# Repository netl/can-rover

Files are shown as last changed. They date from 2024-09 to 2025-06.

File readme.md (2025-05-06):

# can-rover

The goal is to convert cheap RC car kits in to computer driven robots by
replacing the receiver with a separate module.  
The project consists of three parts working as a whole:

1. [Hardware](#hardware)
2. [Firmware](#firmware)
3. [ROS2 node](#ros2-node)

## Hardware

features:

* XT60 passthrough
* fuse protected battery input
* battery current & voltage measurement
    * maximum rating: 20 V, 30 A
    * a charge current of 10 A max can be measured
* 2x canbus+power connectors
* 8 buffered servo channels
* 8 selectable addresses
* 8 buffered inputs with pull-up to 5V
* e-stop controlled servo power

### CAN header

Jumper for 120R termination.  
May be used to power low power stuff. Connector rated at 3 A.  

|pin|  signal |
|---|---|
| 1 | GND |
| 2 | Battery |
| 3 | CAN\_L  |
| 4 | CAN\_H  |

## Firmware

* can-utils: `sudo ip link set up can0 type can bitrate 500000`
* All messages are `big-endian`. 
* [python-can](https://python-can.readthedocs.io/en/stable/scripts.html) has great tools for debugging.
* build with `cd firmware; make`

### CAN messages

`base_address` is selectable by rotary switch. All messages have an offset from that address.
```c
uint8_t arbitration_id = base_address << 8; // address 0 would be: 0x000 and 7: 0x070
```

offset  |parameter       |I/O|bytes
--------|----------------|---|-----
0x0     | servo 1        | I | 1
...     | servo ...      | I | 1
0x7     | servo 8        | I | 1
0x8     | battery Voltage| O | 2
0x9     | battery Current| O | 2
0xa     | sensors 1 .. 8 | O | 1

### Servo

PWM in `1 µs` resolution and if channel hasn't been set within `1 s` it will default to `1500 µs`. For example: `servo 3` with `base_address = 5` would be set to `-90°` with:

```bash
$ cansend can0 052#3e8
```

### Battery monitor

Analog signals directly from A/D, maximum: `4095`

### Inputs

One byte where each bit represents an input

```c
bool value = inputs >> n-1 & 0x1;
```

## ROS2 node
Provided node bridges firmware to ros topics.

### Installation

1. Install [ROS2](https://docs.ros.org/en/jazzy/Installation.html)
2. create [ros2_ws](https://docs.ros.org/en/jazzy/Tutorials/Beginner-Client-Libraries/Creating-A-Workspace/Creating-A-Workspace.html)

```bash
apt install python3-rosdep python3-colcon-common-extensions
ln -s ros2_can_rover ~/ros2_ws/src/can_rover
cd ~/ros2_ws/
colcon build
source install/setup.bash
rosdep init
rosdep update
rosdep install --from-paths src -y --ignore-src
ros2 run can_rover can_rover
```

### Topics and parameters

Interfaces provided are bare minimum for simplicity

topic                      |type     |publish / subscribe|min   |max  |
---------------------------|---------|-------------------|------|-----|
`/rover/voltage`           |[Float32]|subscribe          |0   \*|20\* |
`/rover/current`           |[Float32]|subscribe          |-10 \*|30\* |
`/rover/watts`             |[Float32]|subscribe          |-200\*|600\*|
`/rover/wattHours`         |[Float32]|publish & subscribe|      |     |
`/rover/channel_<n>`       |[Float32]|publish            | -1   | 1   |
`/rover/input_<n>`         |[Bool]   |subscribe          | 0    | 1   |

*\*min/max values limited hardware tolerances and calibration*

parameter                  |type     |default   |
---------------------------|---------|----------|
`/rover/voltage_scale`     |[Float32]|20 / 2^12 |
`/rover/voltage_offset`    |[Float32]|0         |
`/rover/current_scale`     |[Float32]|-40 / 2^12|
`/rover/current_offset`    |[Float32]|10        |
`/rover/channel_<n>_scale` |[Float32]|500       |
`/rover/channel_<n>_offset`|[Float32]|1500      |

[Float32]:https://github.com/ros2/example_interfaces/blob/master/msg/Float32.msg
[Bool]:https://github.com/ros2/example_interfaces/blob/master/msg/Bool.msg

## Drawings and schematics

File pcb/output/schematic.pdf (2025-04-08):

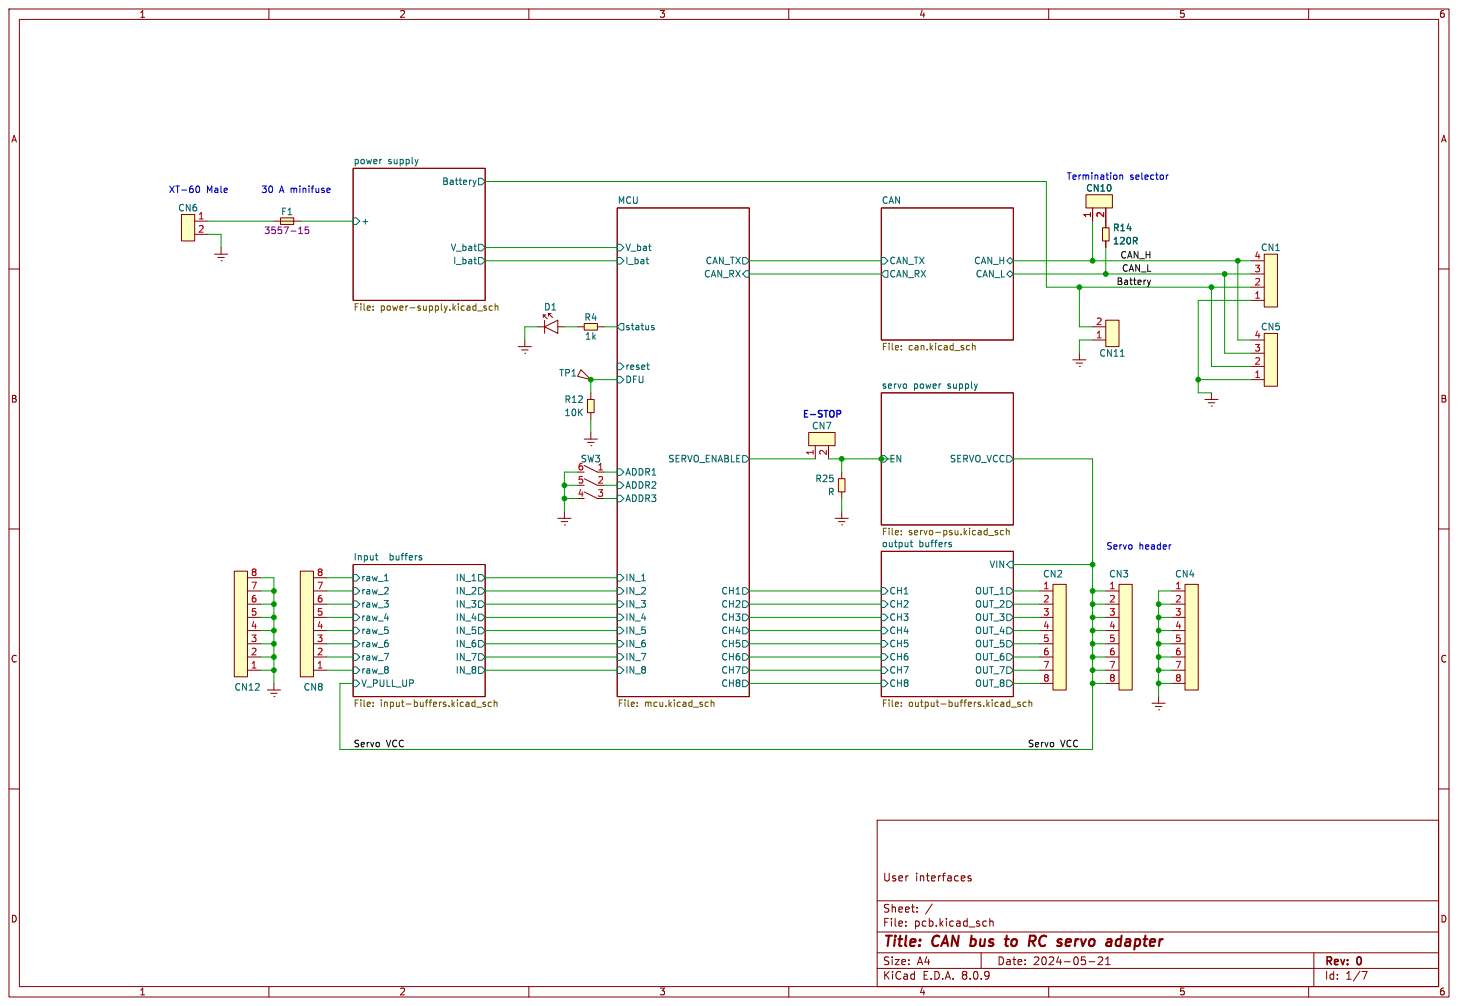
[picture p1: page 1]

output buffers File: output-buffers.kicad_sch

Id: 1/7 Title: CAN bus to RC servo adapter File: pcb.kicad_sch Sheet: / User interfaces

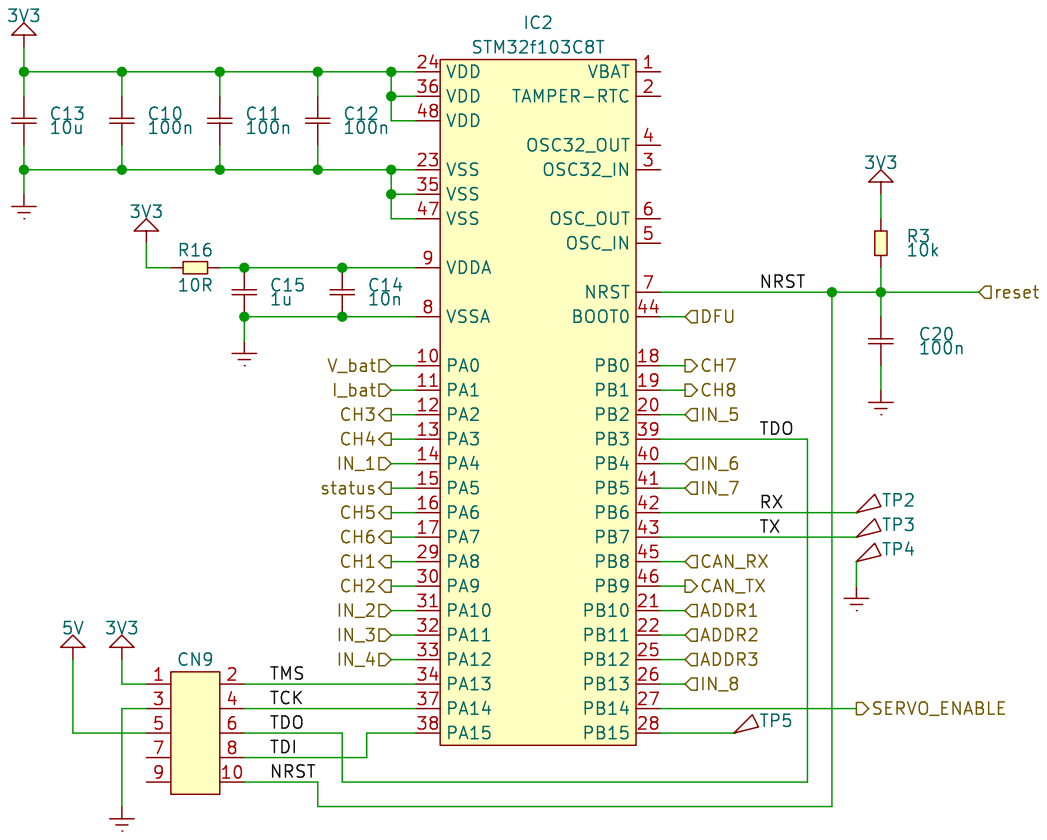
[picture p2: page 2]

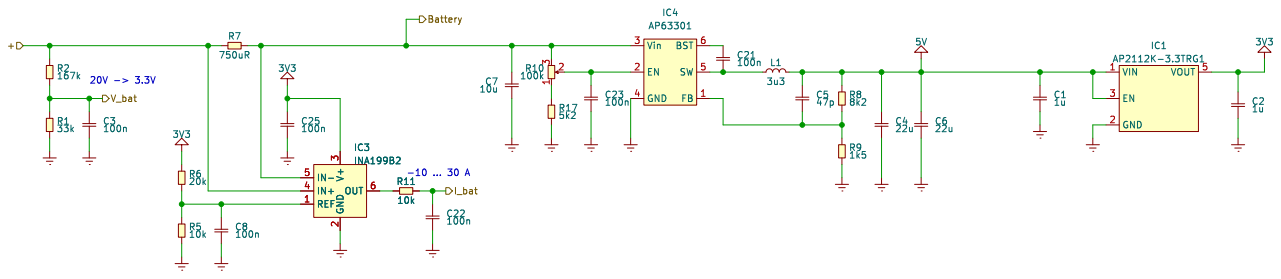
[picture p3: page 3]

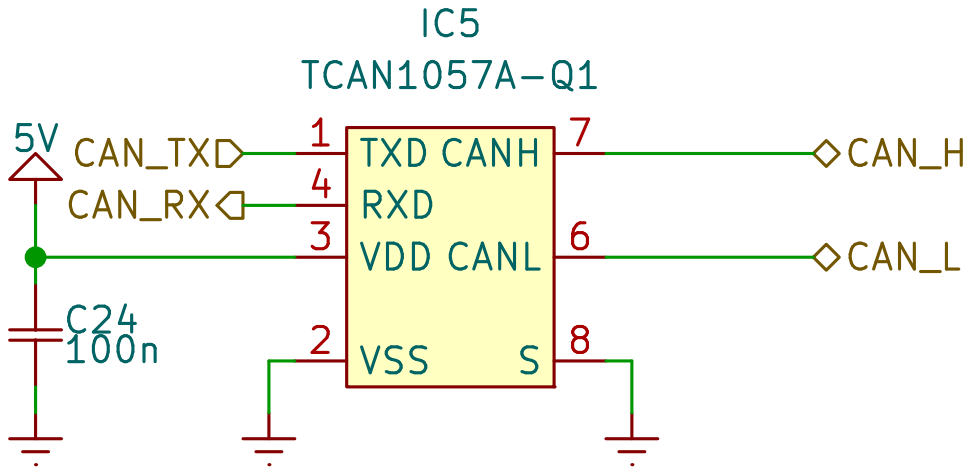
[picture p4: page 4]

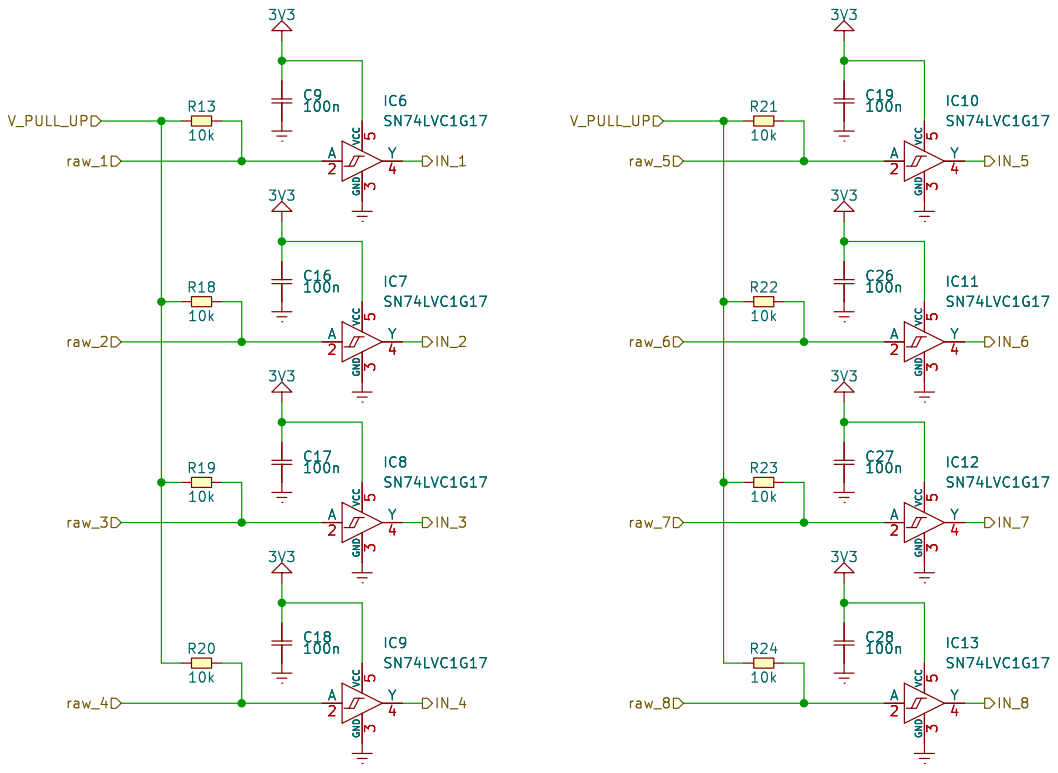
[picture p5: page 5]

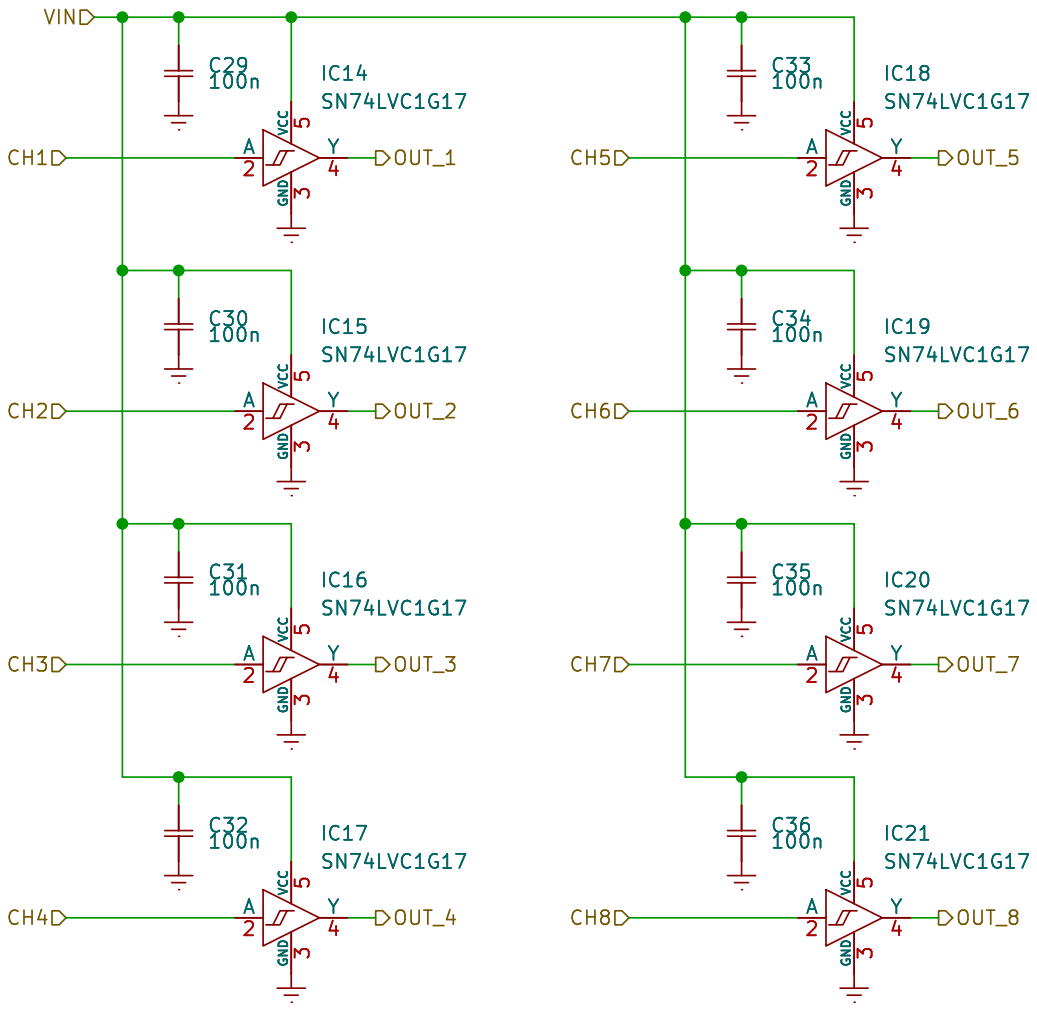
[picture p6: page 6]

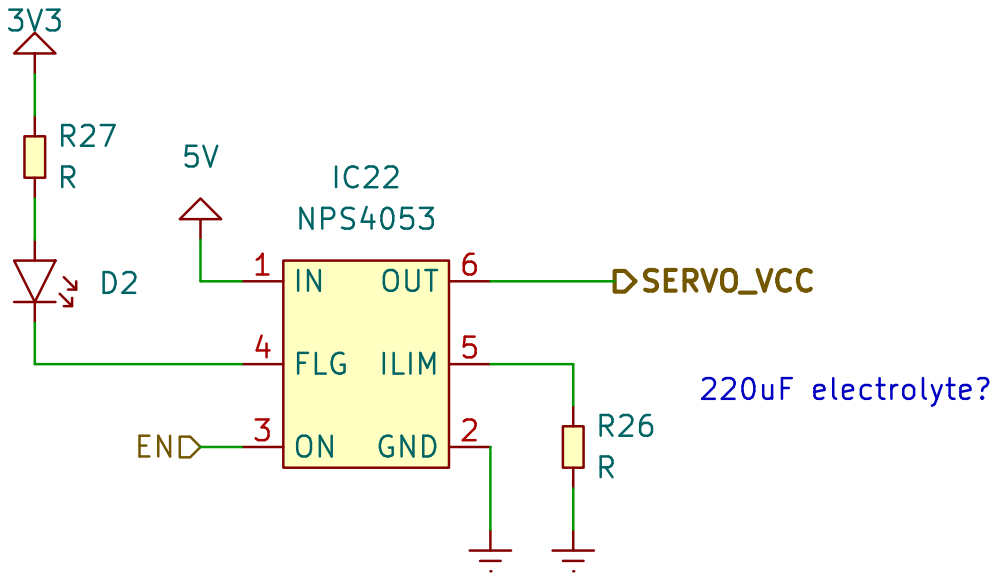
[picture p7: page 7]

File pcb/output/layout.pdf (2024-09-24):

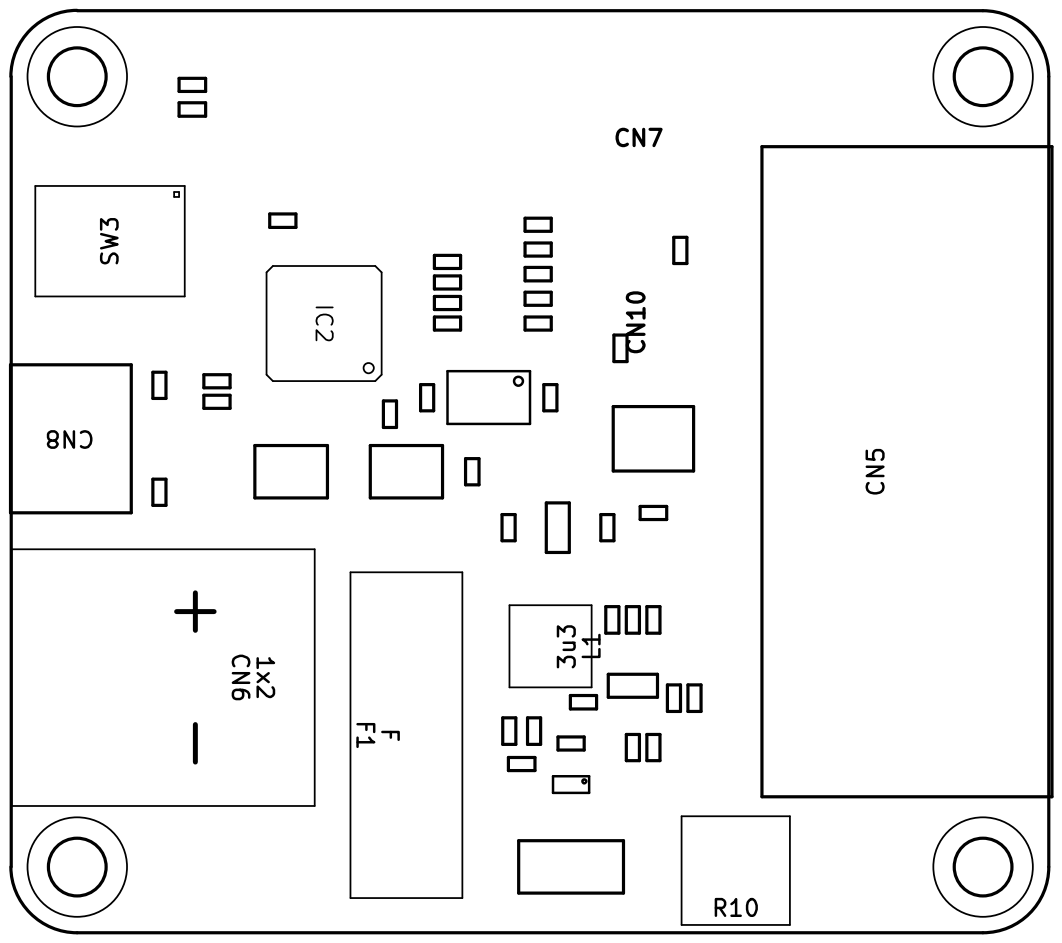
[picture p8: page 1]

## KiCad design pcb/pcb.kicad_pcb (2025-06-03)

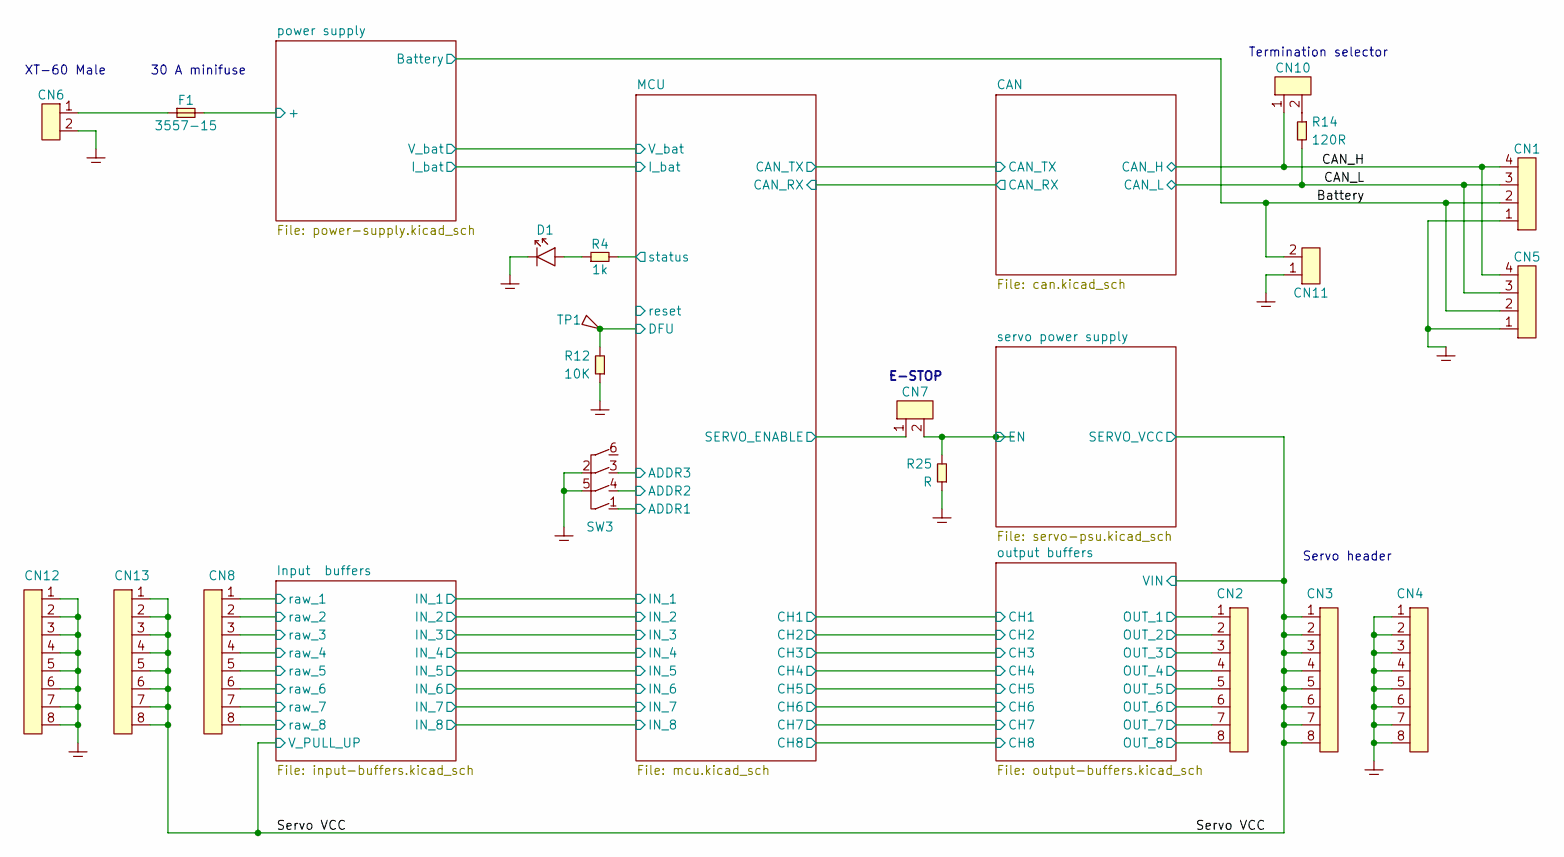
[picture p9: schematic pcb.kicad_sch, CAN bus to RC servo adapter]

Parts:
CN1, CN5: 1x4; jst-xh-4; MPN B4B-XH-A; DigiKey 455-B4B-XH-A-ND
CN2, CN3, CN4, CN8, CN12, CN13: 1x8
CN6, CN11: 1x2; XT60
CN7, CN10: 1x2
D1: LED; 0603
F1: F; 3557-15; MPN 3557-15; DigiKey 36-3557-15-ND
R4: 1k; 0603
R12: 10K; 0603
R14: 120R; 0603
R25: R; 0603
SW3: RD10RA8RTT; MPN RD10RA8RTT; Digi-Key 2449-RD10RA8RTT-ND
TP1: test_point

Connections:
/Battery: CN1.2, CN5.2, CN11.2; also elsewhere on the board
/CAN_H: CN1.4, CN5.4, CN10.1; also elsewhere on the board
/CAN_L: CN1.3, CN5.3, R14.2; also elsewhere on the board
/Input buffers/raw_1: CN8.1; also elsewhere on the board
/Input buffers/raw_2: CN8.2; also elsewhere on the board
/Input buffers/raw_3: CN8.3; also elsewhere on the board
/Input buffers/raw_4: CN8.4; also elsewhere on the board
/Input buffers/raw_5: CN8.5; also elsewhere on the board
/Input buffers/raw_6: CN8.6; also elsewhere on the board
/Input buffers/raw_7: CN8.7; also elsewhere on the board
/Input buffers/raw_8: CN8.8; also elsewhere on the board
/MCU/ADDR1: SW3.1; also elsewhere on the board
/MCU/ADDR2: SW3.4; also elsewhere on the board
/MCU/ADDR3: SW3.3; also elsewhere on the board
/MCU/DFU: R12.2, TP1.1 (TP); also elsewhere on the board
/MCU/SERVO_ENABLE: CN7.1; also elsewhere on the board
/MCU/status: R4.2; also elsewhere on the board
/Servo VCC: CN3.1, CN3.2, CN3.3, CN3.4, CN3.5, CN3.6, CN3.7, CN3.8, CN13.1, CN13.2, CN13.3, CN13.4, CN13.5, CN13.6, CN13.7, CN13.8; also elsewhere on the board
/output buffers/OUT_1: CN2.1; also elsewhere on the board
/output buffers/OUT_2: CN2.2; also elsewhere on the board
/output buffers/OUT_3: CN2.3; also elsewhere on the board
/output buffers/OUT_4: CN2.4; also elsewhere on the board
/output buffers/OUT_5: CN2.5; also elsewhere on the board
/output buffers/OUT_6: CN2.6; also elsewhere on the board
/output buffers/OUT_7: CN2.7; also elsewhere on the board
/output buffers/OUT_8: CN2.8; also elsewhere on the board
/power supply/+: F1.2; also elsewhere on the board
/servo power supply/EN: CN7.2, R25.2; also elsewhere on the board
GND: CN1.1, CN4.1, CN4.2, CN4.3, CN4.4, CN4.5, CN4.6, CN4.7, CN4.8, CN5.1, CN6.2, CN11.1, CN12.1, CN12.2, CN12.3, CN12.4, CN12.5, CN12.6, CN12.7, CN12.8, D1.2 (K), R12.1, R25.1, SW3.2, SW3.5; also elsewhere on the board
unnamed: CN6.1, F1.1
unnamed: CN10.2, R14.1
unnamed: D1.1 (A), R4.1

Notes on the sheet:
30 A minifuse
E-STOP
Termination selector
Servo header
XT-60 Male

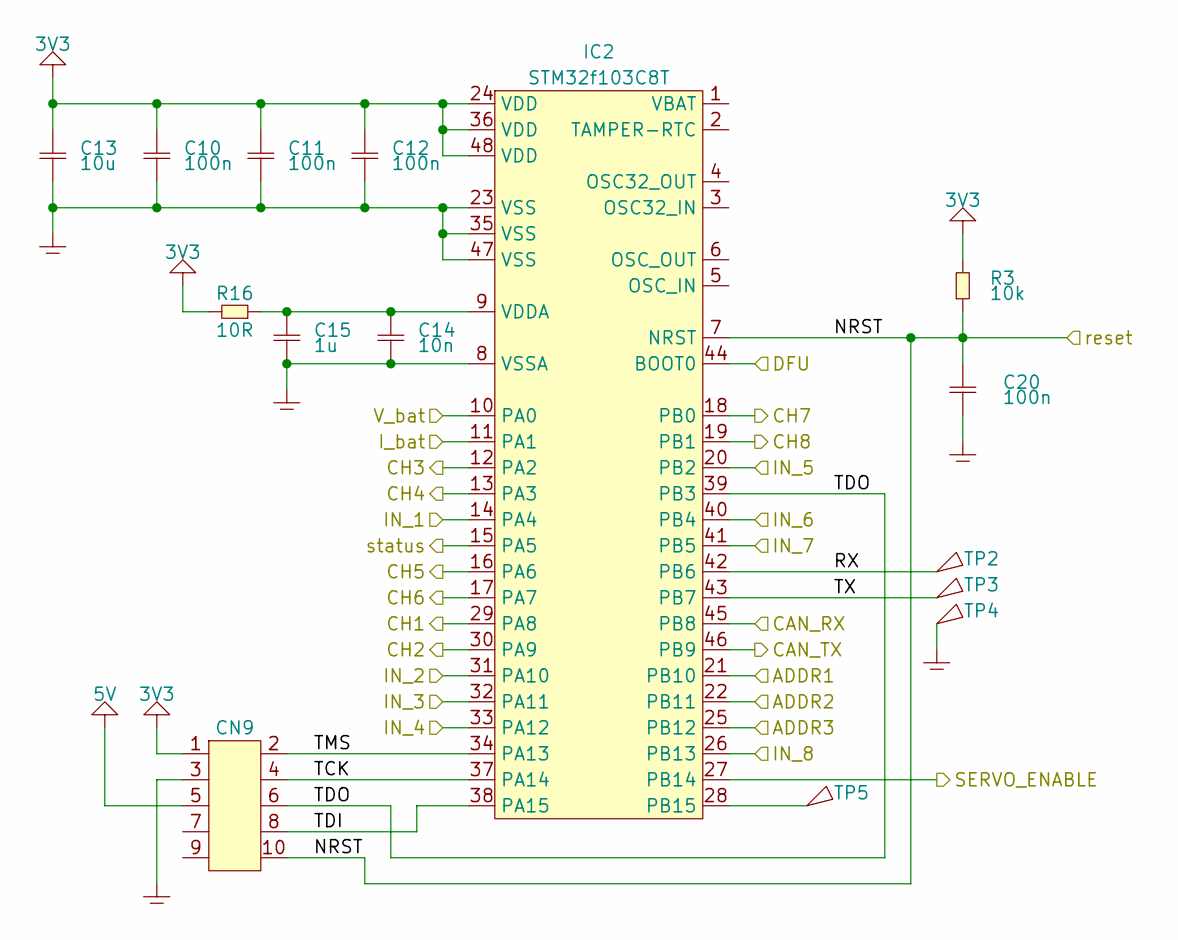
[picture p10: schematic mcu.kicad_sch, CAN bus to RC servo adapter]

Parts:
C10, C11, C12, C20: 100n; 0603
C13: 10u; 0603
C14: 10n; 0603
C15: 1u; 0603
CN9: 2x5; 2x5_test_points
IC2: STM32f103C8T; LQFP-48; MPN STM32F103C8T6TR; DigiKey 497-17666-1-ND
R3: 10k; 0603
R16: 10R; 0603
TP2, TP3, TP4, TP5: test_point

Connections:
3V3: C10.1, C11.1, C12.1, C13.1, CN9.1, IC2.24 (VDD), IC2.36 (VDD), IC2.48 (VDD), R3.2, R16.2; also elsewhere on the board
5V: CN9.5; also elsewhere on the board
/CAN/CAN_RX: IC2.45 (PB8); also elsewhere on the board
/CAN/CAN_TX: IC2.46 (PB9); also elsewhere on the board
/Input buffers/IN_1: IC2.14 (PA4); also elsewhere on the board
/Input buffers/IN_2: IC2.31 (PA10); also elsewhere on the board
/Input buffers/IN_3: IC2.32 (PA11); also elsewhere on the board
/Input buffers/IN_4: IC2.33 (PA12); also elsewhere on the board
/Input buffers/IN_5: IC2.20 (PB2); also elsewhere on the board
/Input buffers/IN_6: IC2.40 (PB4); also elsewhere on the board
/Input buffers/IN_7: IC2.41 (PB5); also elsewhere on the board
/Input buffers/IN_8: IC2.26 (PB13); also elsewhere on the board
/MCU/ADDR1: IC2.21 (PB10); also elsewhere on the board
/MCU/ADDR2: IC2.22 (PB11); also elsewhere on the board
/MCU/ADDR3: IC2.25 (PB12); also elsewhere on the board
/MCU/CH1: IC2.29 (PA8); also elsewhere on the board
/MCU/CH2: IC2.30 (PA9); also elsewhere on the board
/MCU/CH3: IC2.12 (PA2); also elsewhere on the board
/MCU/CH4: IC2.13 (PA3); also elsewhere on the board
/MCU/CH5: IC2.16 (PA6); also elsewhere on the board
/MCU/CH6: IC2.17 (PA7); also elsewhere on the board
/MCU/CH7: IC2.18 (PB0); also elsewhere on the board
/MCU/CH8: IC2.19 (PB1); also elsewhere on the board
/MCU/DFU: IC2.44 (BOOT0); also elsewhere on the board
/MCU/I_bat: IC2.11 (PA1); also elsewhere on the board
/MCU/NRST: C20.1, CN9.10, IC2.7 (NRST), R3.1
/MCU/RX: IC2.42 (PB6), TP2.1 (TP)
/MCU/SERVO_ENABLE: IC2.27 (PB14); also elsewhere on the board
/MCU/TCK: CN9.4, IC2.37 (PA14)
/MCU/TDI: CN9.8, IC2.38 (PA15)
/MCU/TDO: CN9.6, IC2.39 (PB3)
/MCU/TMS: CN9.2, IC2.34 (PA13)
/MCU/TX: IC2.43 (PB7), TP3.1 (TP)
/MCU/V_bat: IC2.10 (PA0); also elsewhere on the board
/MCU/status: IC2.15 (PA5); also elsewhere on the board
GND: C10.2, C11.2, C12.2, C13.2, C14.2, C15.2, C20.2, CN9.3, IC2.8 (VSSA), IC2.23 (VSS), IC2.35 (VSS), IC2.47 (VSS), TP4.1 (TP); also elsewhere on the board
unnamed: IC2.28 (PB15), TP5.1 (TP)
unnamed: C14.1, C15.1, IC2.9 (VDDA), R16.1

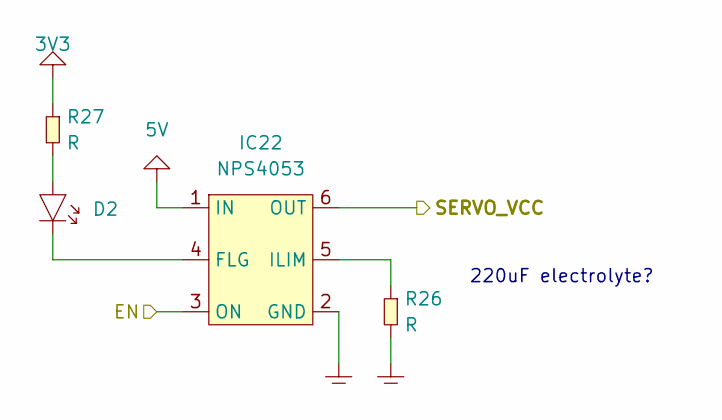
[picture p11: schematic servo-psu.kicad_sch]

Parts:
D2: LED; 0603
IC22: NPS4053; SOT-23-6; MPN NPS4053GVH; DigiKey 1727-NPS4053GVHCT-ND
R26, R27: R; 0603

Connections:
3V3: R27.1; also elsewhere on the board
5V: IC22.1 (IN); also elsewhere on the board
/Servo VCC: IC22.6 (OUT); also elsewhere on the board
/servo power supply/EN: IC22.3 (ON); also elsewhere on the board
GND: IC22.2 (GND), R26.2; also elsewhere on the board
unnamed: D2.1 (A), R27.2
unnamed: D2.2 (K), IC22.4 (FLG)
unnamed: IC22.5 (ILIM), R26.1

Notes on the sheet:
220uF electrolyte?

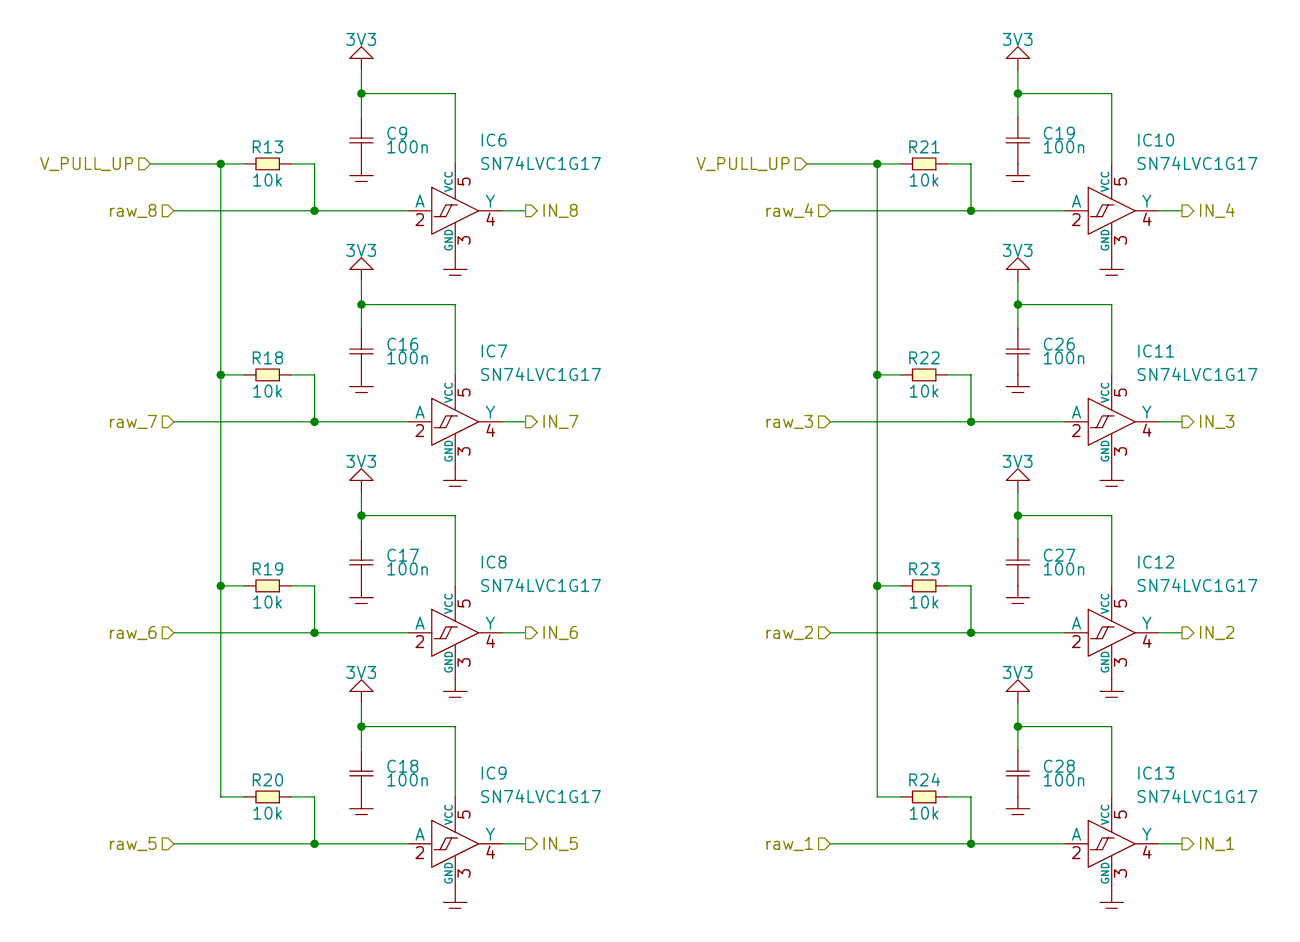
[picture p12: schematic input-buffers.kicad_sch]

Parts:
C9, C16, C17, C18, C19, C26, C27, C28: 100n; 0603
IC6, IC7, IC8, IC9, IC10, IC11, IC12, IC13: SN74LVC1G17; SC70-5L
R13, R18, R19, R20, R21, R22, R23, R24: 10k; 0603

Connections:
3V3: C9.2, C16.2, C17.2, C18.2, C19.2, C26.2, C27.2, C28.2, IC6.5 (VCC), IC7.5 (VCC), IC8.5 (VCC), IC9.5 (VCC), IC10.5 (VCC), IC11.5 (VCC), IC12.5 (VCC), IC13.5 (VCC); also elsewhere on the board
/Input buffers/IN_1: IC13.4 (Y); also elsewhere on the board
/Input buffers/IN_2: IC12.4 (Y); also elsewhere on the board
/Input buffers/IN_3: IC11.4 (Y); also elsewhere on the board
/Input buffers/IN_4: IC10.4 (Y); also elsewhere on the board
/Input buffers/IN_5: IC9.4 (Y); also elsewhere on the board
/Input buffers/IN_6: IC8.4 (Y); also elsewhere on the board
/Input buffers/IN_7: IC7.4 (Y); also elsewhere on the board
/Input buffers/IN_8: IC6.4 (Y); also elsewhere on the board
/Input buffers/raw_1: IC13.2 (A), R24.1; also elsewhere on the board
/Input buffers/raw_2: IC12.2 (A), R23.1; also elsewhere on the board
/Input buffers/raw_3: IC11.2 (A), R22.1; also elsewhere on the board
/Input buffers/raw_4: IC10.2 (A), R21.1; also elsewhere on the board
/Input buffers/raw_5: IC9.2 (A), R20.1; also elsewhere on the board
/Input buffers/raw_6: IC8.2 (A), R19.1; also elsewhere on the board
/Input buffers/raw_7: IC7.2 (A), R18.1; also elsewhere on the board
/Input buffers/raw_8: IC6.2 (A), R13.1; also elsewhere on the board
/Servo VCC: R13.2, R18.2, R19.2, R20.2, R21.2, R22.2, R23.2, R24.2; also elsewhere on the board
GND: C9.1, C16.1, C17.1, C18.1, C19.1, C26.1, C27.1, C28.1, IC6.3 (GND), IC7.3 (GND), IC8.3 (GND), IC9.3 (GND), IC10.3 (GND), IC11.3 (GND), IC12.3 (GND), IC13.3 (GND); also elsewhere on the board

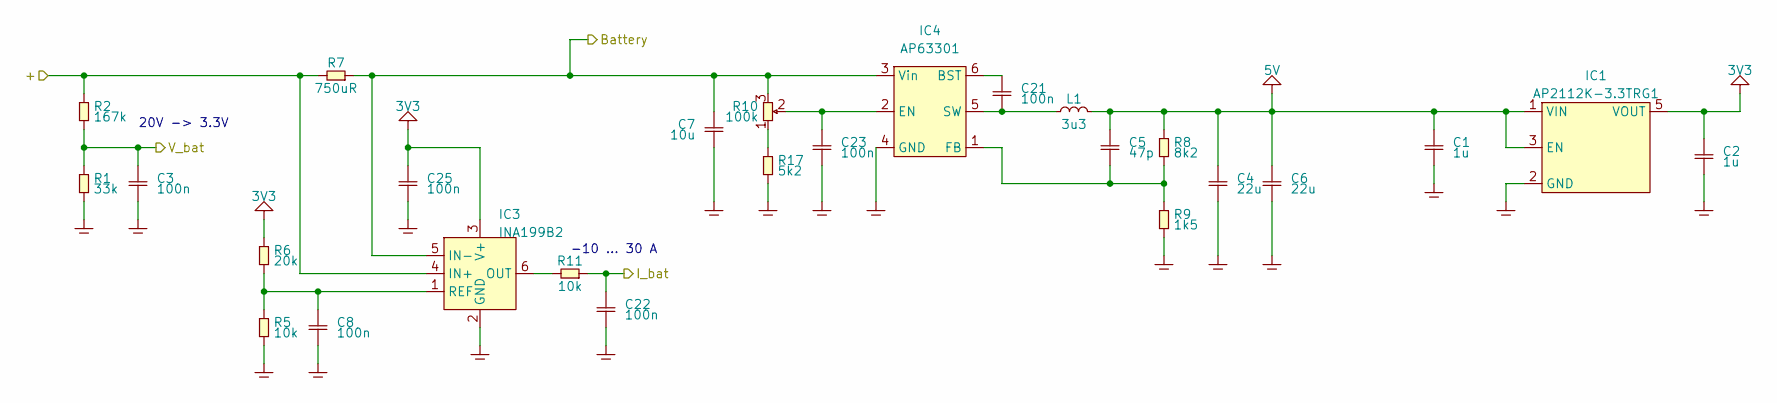
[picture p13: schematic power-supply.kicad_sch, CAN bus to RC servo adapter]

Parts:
C1, C2: 1u; 0603
C3, C8, C21, C22, C23, C25: 100n; 0603
C4, C6: 22u; 0603
C5: 47p; 0603
C7: 10u; 0603
IC1: AP2112K-3.3TRG1; SOT-23-5; MPN AP2112K-3.3TRG1; Digi-Key AP2112K-3.3TRG1DICT-ND
IC3: INA199B2; SC70-6L; MPN INA199B2DCKR; DigiKey 296-40119-1-ND
IC4: AP63301; TSOT-26; MPN AP63301WU-7; DigiKey 31-AP63301WU-7CT-ND
L1: 3u3; 5x5; MPN VLS5045EX-3R3N; DigiKey 445-174398-1-ND
R1: 33k; 0603
R2: 167k; 0603
R5, R11: 10k; 0603
R6: 20k; 0603
R7: 750uR; 2512-high-current
R8: 8k2; 0603
R9: 1k5; 0603
R10: 100k; 3362P; MPN 3362P-1-104LF; DigiKey 3362P-104LF-ND
R17: 5k2; 0603

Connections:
3V3: C2.1, C25.1, IC1.5 (VOUT), IC3.3 (V+), R6.2; also elsewhere on the board
5V: C1.1, C4.1, C5.1, C6.1, IC1.1 (VIN), IC1.3 (EN), L1.2, R8.2; also elsewhere on the board
/Battery: C7.1, IC3.5 (IN-), IC4.3 (Vin), R7.1, R10.3; also elsewhere on the board
/MCU/I_bat: C22.1, R11.1; also elsewhere on the board
/MCU/V_bat: C3.1, R1.2, R2.1; also elsewhere on the board
/power supply/+: IC3.4 (IN+), R2.2, R7.2; also elsewhere on the board
GND: C1.2, C2.2, C3.2, C4.2, C6.2, C7.2, C8.2, C22.2, C23.2, C25.2, IC1.2 (GND), IC3.2 (GND), IC4.4 (GND), R1.1, R5.1, R9.1, R17.1; also elsewhere on the board
unnamed: IC3.6 (OUT), R11.2
unnamed: C8.1, IC3.1 (REF), R5.2, R6.1
unnamed: C21.1, IC4.6 (BST)
unnamed: C23.1, IC4.2 (EN), R10.2
unnamed: C5.2, IC4.1 (FB), R8.1, R9.2
unnamed: C21.2, IC4.5 (SW), L1.1
unnamed: R10.1, R17.2

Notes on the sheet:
-10 ... 30 A
20V -> 3.3V

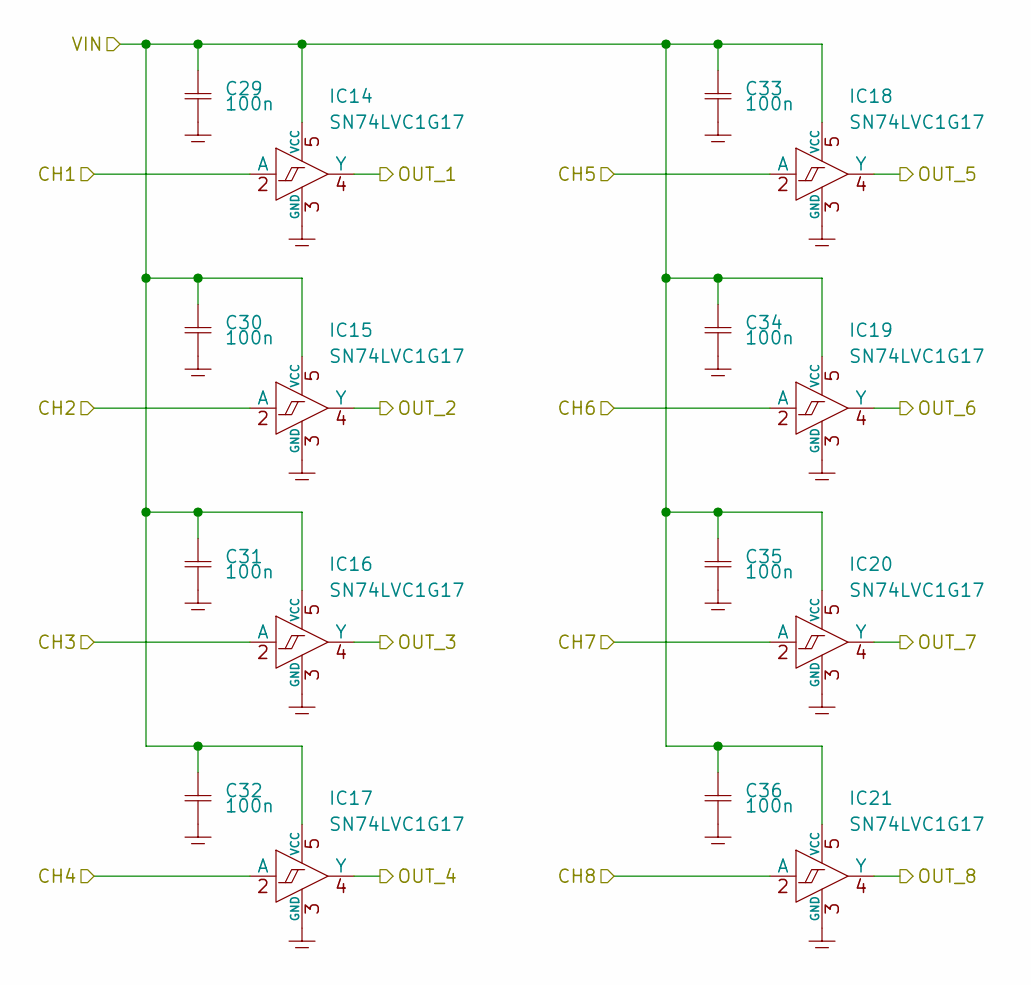
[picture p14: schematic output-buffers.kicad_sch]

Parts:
C29, C30, C31, C32, C33, C34, C35, C36: 100n; 0603
IC14, IC15, IC16, IC17, IC18, IC19, IC20, IC21: SN74LVC1G17; SC70-5L

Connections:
/MCU/CH1: IC14.2 (A); also elsewhere on the board
/MCU/CH2: IC15.2 (A); also elsewhere on the board
/MCU/CH3: IC16.2 (A); also elsewhere on the board
/MCU/CH4: IC17.2 (A); also elsewhere on the board
/MCU/CH5: IC18.2 (A); also elsewhere on the board
/MCU/CH6: IC19.2 (A); also elsewhere on the board
/MCU/CH7: IC20.2 (A); also elsewhere on the board
/MCU/CH8: IC21.2 (A); also elsewhere on the board
/Servo VCC: C29.2, C30.2, C31.2, C32.2, C33.2, C34.2, C35.2, C36.2, IC14.5 (VCC), IC15.5 (VCC), IC16.5 (VCC), IC17.5 (VCC), IC18.5 (VCC), IC19.5 (VCC), IC20.5 (VCC), IC21.5 (VCC); also elsewhere on the board
/output buffers/OUT_1: IC14.4 (Y); also elsewhere on the board
/output buffers/OUT_2: IC15.4 (Y); also elsewhere on the board
/output buffers/OUT_3: IC16.4 (Y); also elsewhere on the board
/output buffers/OUT_4: IC17.4 (Y); also elsewhere on the board
/output buffers/OUT_5: IC18.4 (Y); also elsewhere on the board
/output buffers/OUT_6: IC19.4 (Y); also elsewhere on the board
/output buffers/OUT_7: IC20.4 (Y); also elsewhere on the board
/output buffers/OUT_8: IC21.4 (Y); also elsewhere on the board
GND: C29.1, C30.1, C31.1, C32.1, C33.1, C34.1, C35.1, C36.1, IC14.3 (GND), IC15.3 (GND), IC16.3 (GND), IC17.3 (GND), IC18.3 (GND), IC19.3 (GND), IC20.3 (GND), IC21.3 (GND); also elsewhere on the board

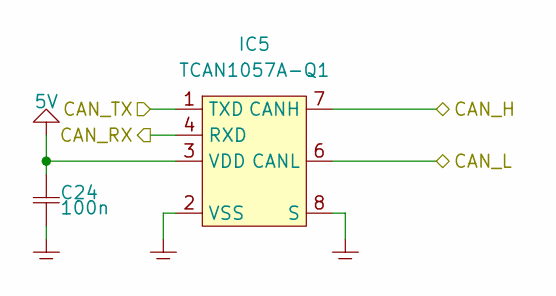
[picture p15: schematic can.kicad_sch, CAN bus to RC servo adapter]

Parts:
C24: 100n; 0603
IC5: TCAN1057A-Q1; TSOT-23-8; MPN TCAN1057AVDDFRQ1; DigiKey 296-TCAN1057AVDDFRQ1CT-ND

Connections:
5V: C24.1, IC5.3 (VDD); also elsewhere on the board
/CAN/CAN_RX: IC5.4 (RXD); also elsewhere on the board
/CAN/CAN_TX: IC5.1 (TXD); also elsewhere on the board
/CAN_H: IC5.7 (CANH); also elsewhere on the board
/CAN_L: IC5.6 (CANL); also elsewhere on the board
GND: C24.2, IC5.2 (VSS), IC5.8 (S); also elsewhere on the board

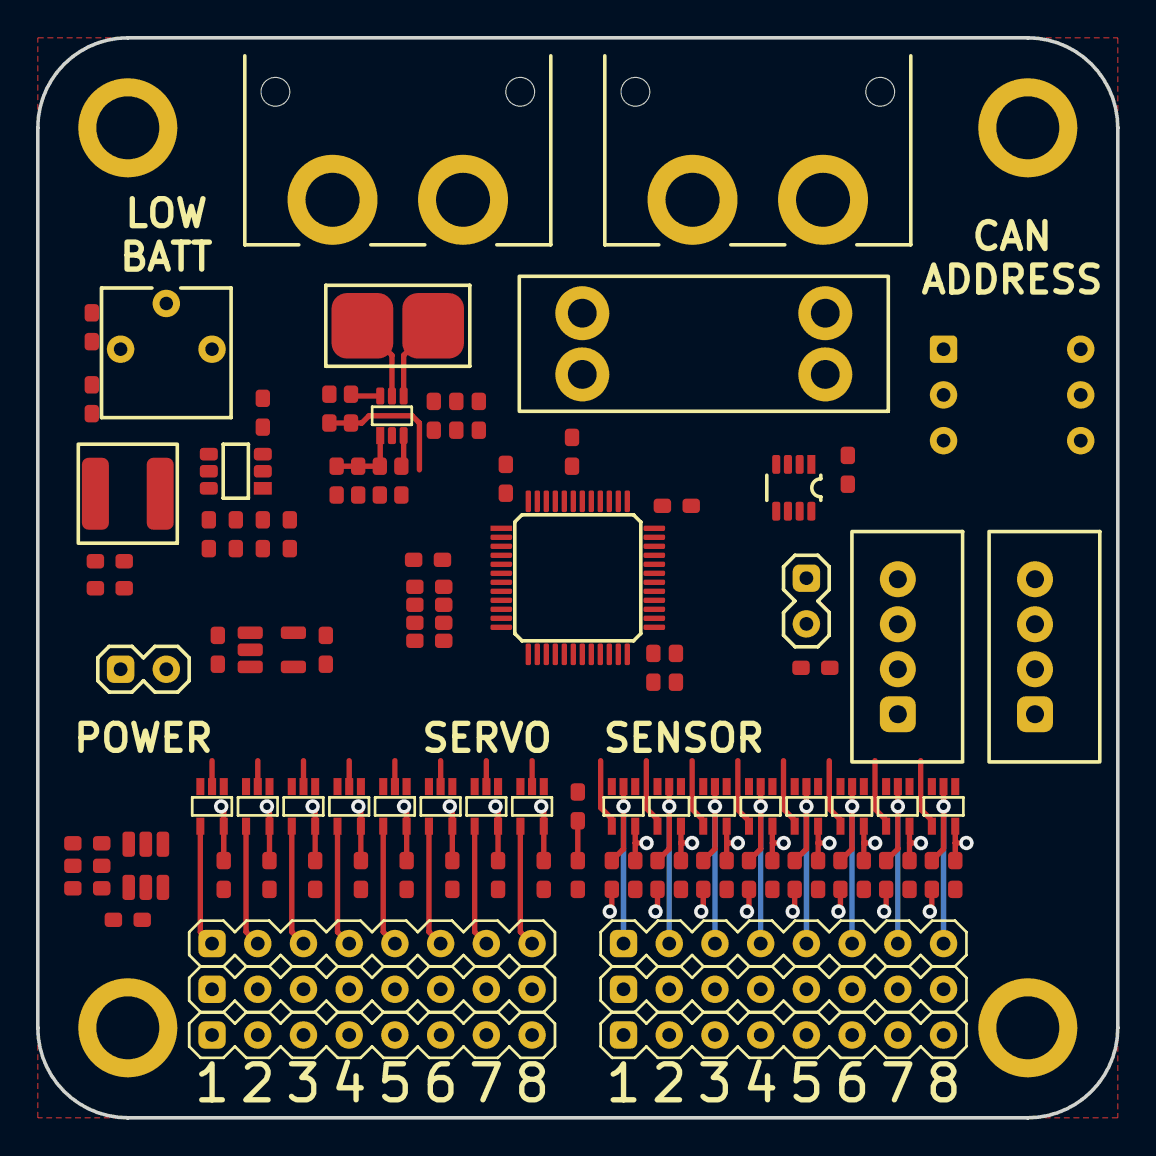
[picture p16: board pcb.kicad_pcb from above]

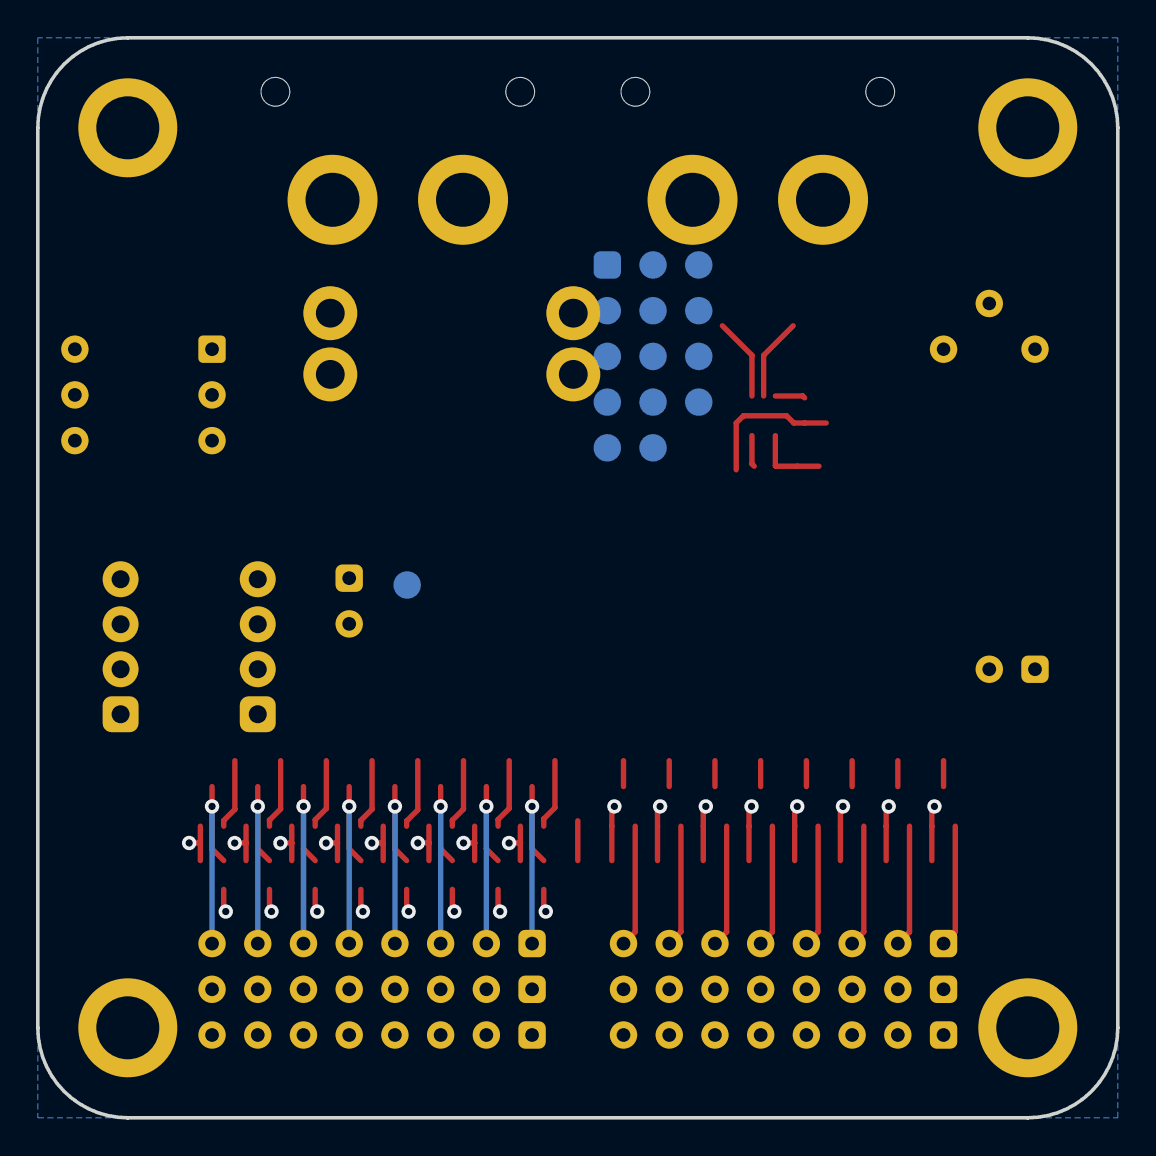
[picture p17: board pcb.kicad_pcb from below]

Board: 4 copper layers, 60.0 x 60.0 mm, 107 parts (6 on the bottom side), 73 nets.

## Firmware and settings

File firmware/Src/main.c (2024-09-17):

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
/* Includes ------------------------------------------------------------------*/
#include "main.h"

/* USER CODE BEGIN PD */
#define BASE_CHANNEL_ID 0x010 //TODO: Read from DIP switches
#define N_CHANNELS 8
#define SERVO_CENTER 1500
#define SAFETY_TIMEOUT 2000
#define CAN_MESSAGES 2 //number of different messages to send over CAN bus

/* USER CODE END PD */

ADC_HandleTypeDef hadc1;
DMA_HandleTypeDef hdma_adc1;

CAN_HandleTypeDef hcan;

TIM_HandleTypeDef htim1;
TIM_HandleTypeDef htim2;
TIM_HandleTypeDef htim3;

/* USER CODE BEGIN PV */
//CAN bus
CAN_RxHeaderTypeDef rxHeader; //Transmit Header
CAN_TxHeaderTypeDef txHeader; //Receive Header
uint8_t canRX[8] = {0,0,0,0,0,0,0,0};  //Receive Buffer
CAN_FilterTypeDef canfil; //Filter
uint32_t canMailbox; //Mail box variable
uint32_t CANAddress;

//Servo
uint32_t servoLastUpdated[N_CHANNELS] = {0}; //timestamps for timeout

//ADC
uint32_t ADCResults[2] = {0,0}; //ADC results
/* USER CODE END PV */

void SystemClock_Config(void);
static void MX_GPIO_Init(void);
static void MX_DMA_Init(void);
static void MX_ADC1_Init(void);
static void MX_CAN_Init(void);
static void MX_TIM1_Init(void);
static void MX_TIM2_Init(void);
static void MX_TIM3_Init(void);
/* USER CODE BEGIN PFP */
void setServo(uint8_t channel, uint16_t value);

/* USER CODE END PFP */

/**
  * @brief  The application entry point.
  * @retval int
  */
int main(void)
{
  /* MCU Configuration--------------------------------------------------------*/

  /* Reset of all peripherals, Initializes the Flash interface and the Systick. */
  HAL_Init();

  /* Configure the system clock */
  SystemClock_Config();

  /* Initialize all configured peripherals */
  MX_GPIO_Init();
  MX_DMA_Init();
  MX_ADC1_Init();
  MX_CAN_Init();
  MX_TIM1_Init();
  MX_TIM2_Init();
  MX_TIM3_Init();
  /* USER CODE BEGIN 2 */

  //setup servos
  for(int i=0; i<N_CHANNELS; i++)
    setServo(i, SERVO_CENTER);
  /* USER CODE END 2 */

  /* Infinite loop */
  /* USER CODE BEGIN WHILE */
  uint32_t txMailbox;
  while (1)
  {
    HAL_GPIO_WritePin(status_GPIO_Port, status_Pin, GPIO_PIN_SET);

    //transmit status
    if (HAL_CAN_GetTxMailboxesFreeLevel(&hcan) > 0){
            //set address
            static uint8_t TXCounter = 0;
            uint8_t data[2] = {0};
            txHeader.StdId = CANAddress | 0x8 | (TXCounter & 0b111);

            //fetch correct data
            switch(TXCounter){
                case 0: //battery voltage
                    data[1] = ADCResults[0] & 0xff;
                    data[0] = (ADCResults[0]>>8) & 0xff;
                    break;
                case 1: //battery current
                    data[1] = ADCResults[1] & 0xff;
                    data[0] = (ADCResults[1]>>8) & 0xff;
                    break;
            }

            //send
            HAL_CAN_AddTxMessage(&hcan, &txHeader, data, &txMailbox);

            //next address
            TXCounter++;
            if (TXCounter > CAN_MESSAGES-1)
                TXCounter = 0;
    }

    HAL_ADC_Start_DMA(&hadc1, ADCResults, 2); // start adc in DMA mode

    //center any channel that hasn't been updated for a while
    for(int i=0; i<N_CHANNELS; i++){
        if ( (HAL_GetTick() - servoLastUpdated[i]) > SAFETY_TIMEOUT)
            setServo(i, SERVO_CENTER);
    }

    HAL_GPIO_WritePin(status_GPIO_Port, status_Pin, GPIO_PIN_RESET);
    HAL_Delay(1000/(CAN_MESSAGES*3));
    /* USER CODE END WHILE */

    /* USER CODE BEGIN 3 */
  }
  /* USER CODE END 3 */
}

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
/* USER CODE BEGIN 4 */
//interrupt for received CAN frame
void HAL_CAN_RxFifo0MsgPendingCallback(CAN_HandleTypeDef *hcan1)
{
    //inform user of received data
    HAL_GPIO_WritePin(status_GPIO_Port, status_Pin, GPIO_PIN_SET);

    //get CAN bus message to canRX buffer
    HAL_CAN_GetRxMessage(hcan1, CAN_RX_FIFO0, &rxHeader, canRX);

    //match arbitration ID to pwm channel
    uint8_t channel = rxHeader.StdId & 0x7;

    //combine bytes
    uint16_t value = canRX[0]<<8 | canRX[1];

    setServo(channel, value);
}

void setServo(uint8_t channel, uint16_t value){
    //match to timer channels
    switch(channel){
        case 0:
            TIM1->CCR1 = value; //PA8
            break;
        case 1:
            TIM1->CCR2 = value; //PA9
            break;
        case 2:
            TIM2->CCR3 = value; //PA2
            break;
        case 3:
            TIM2->CCR4 = value; //PA3
            break;
        case 4:
            TIM3->CCR1 = value; //PA6
            break;
        case 5:
            TIM3->CCR2 = value; //PA7
            break;
        case 6:
            TIM3->CCR3 = value; //PB0
            break;
        case 7:
            TIM3->CCR4 = value; //PB1
            break;
    }
    servoLastUpdated[channel] = HAL_GetTick(); //update for timeout
}

/* USER CODE END 4 */
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


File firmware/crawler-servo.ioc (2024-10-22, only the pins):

Mcu.UserName=STM32F103C8Tx
PA0-WKUP.Signal=ADCx_IN0
PA1.Signal=ADCx_IN1
PA10.GPIO_Label=IN_2
PA10.Signal=GPIO_Input
PA11.GPIO_Label=IN_3
PA11.Signal=GPIO_Input
PA12.GPIO_Label=IN_4
PA12.Signal=GPIO_Input
PA2.Signal=S_TIM2_CH3
PA3.Signal=S_TIM2_CH4
PA4.GPIO_Label=IN_1
PA4.Signal=GPIO_Input
PA5.GPIO_Label=status
PA5.Signal=GPIO_Output
PA6.Signal=S_TIM3_CH1
PA7.Signal=S_TIM3_CH2
PA8.Signal=S_TIM1_CH1
PA9.Signal=S_TIM1_CH2
PB0.Signal=S_TIM3_CH3
PB1.Signal=S_TIM3_CH4
PB10.GPIO_Label=ADDR_1
PB10.Signal=GPIO_Input
PB11.GPIO_Label=ADDR_2
PB11.Signal=GPIO_Input
PB12.GPIO_Label=ADDR_3
PB12.Signal=GPIO_Input
PB13.GPIO_Label=IN_8
PB13.Signal=GPIO_Input
PB2.GPIO_Label=IN_5
PB2.Signal=GPIO_Input
PB4.GPIO_Label=IN_6
PB4.Signal=GPIO_Input
PB5.GPIO_Label=IN_7
PB5.Signal=GPIO_Input
PB8.Signal=CAN_RX
PB9.Signal=CAN_TX

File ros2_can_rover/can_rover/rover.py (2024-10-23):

import rclpy
from rclpy.node import Node
from std_msgs.msg import Float32
import can
from functools import partial
import time

class canRover(Node):
    def __init__(self):
        super().__init__('can_rover')

        #power monitoring
        self.power = {
            "voltage":0,
            "current":0,
            "watts":0,
            "wattHours":0,
            "time":time.time(),
        }

        #parameters
        self.declare_parameter("base_id", 0x10)
        self.declare_parameter("voltage_scale", 20./4096)
        self.declare_parameter("voltage_offset", 0.)
        self.declare_parameter("current_scale", -40./4096)
        self.declare_parameter("current_offset", 10.)
        for n in range(8): #servo channels
            self.declare_parameter(f"channel_{n+1}_scale", 1000)
            self.declare_parameter(f"channel_{n+1}_offset", 1500)

        #publisher
        self.outputs = ["voltage", "current", "watts", "wattHours"]
        self.publishTopics = []
        for topic in self.outputs:
            self.publishTopics.append(self.create_publisher(Float32, f"rover/{topic}", 10))

        #subscriber
        self.subscribeTopics = []
        for channel in range(8):
            self.subscribeTopics.append(self.create_subscription(Float32, f"rover/channel_{channel+1}", partial(self.listener_callback, channel), 10))

        self.setWh = self.create_subscription(Float32,  "rover/set_wattHours", self.set_wattHours, 10)

        #self.subscription # prevent unused variable warning

        #canbus
        base_id = self.get_parameter("base_id").get_parameter_value().integer_value
        canFilter = [{"can_id":0x7f8,"can_mask":base_id | 0x008, "extended":False}]
        self.bus = can.ThreadSafeBus(interface='socketcan', channel='can0', bitrate=500000, can_filters=canFilter)

        #start loop
        self.timer = self.create_timer(0.1, self.can_listener_loop)

    #publish can data 
    def can_listener_loop(self):
        msg = self.bus.recv(timeout=0)
        if msg:
            channel = msg.arbitration_id & 0x007
            if channel not in range(len(self.outputs)):
                return

            value = int.from_bytes(msg.data, "big")
            
            #scale and offset
            topic = self.outputs[channel]
            scale = self.get_parameter(f"{topic}_scale").get_parameter_value().double_value
            offset = self.get_parameter(f"{topic}_offset").get_parameter_value().double_value
            result = value*scale+offset

            #publish
            output = Float32()
            output.data = result
            self.publishTopics[channel].publish(output)
            self.get_logger().debug(f"{topic}:{result}")

            #update power
            self.power.update({topic:result})
            t = time.time()
            w = self.power["voltage"]*self.power["current"]
            self.get_logger().debug(f"watts:{w}")

            #watt hours
            td = (t-self.power["time"])/3600 #time delta in hours
            wt = td*(w+self.power["watts"])/2 #trapezoidal
            wattHours = self.power["wattHours"]+wt
            self.get_logger().debug(f"wattHours:{wattHours}")
            self.power.update({"time":t,"wattHours":wattHours,"watts":w})

            #send
            wOut = Float32()
            wOut.data = w
            wHOut = Float32()
            wHOut.data = wattHours
            self.publishTopics[2].publish(wOut)
            self.publishTopics[3].publish(wHOut)
   
    #set servo channels 
    def listener_callback(self, channel, msg):
        a = msg.data
        scale = self.get_parameter(f"channel_{channel+1}_scale").get_parameter_value().integer_value
        offset = self.get_parameter(f"channel_{channel+1}_offset").get_parameter_value().integer_value
        result = int(a*scale+offset)

        #can address base
        base_id = self.get_parameter("base_id").get_parameter_value().integer_value

        #create can message
        bus_msg = can.Message(is_extended_id=False)
        bus_msg.data = result.to_bytes(2,"big")
        bus_msg.arbitration_id = base_id | channel
        bus_msg.dlc = 2

        #send
        self.bus.send(bus_msg, timeout=0)
        self.get_logger().debug(f"{channel}:{result}")

    def set_wattHours(self, msg):
        self.power.update({"wattHours":msg.data})

def main(args=None):
    rclpy.init(args=args)
    rclpy.spin(canRover())

if __name__ == '__main__':
    main()

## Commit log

2023-08-31 created stm32cubemx project
2023-09-26 pwm now works at 50 hz for some reason
2023-09-28 fixed pwm configuration. ch1 now goes to servo middle
    [crawler-servo.ioc, main.c]
2023-10-31 added command for setting up canbus
2023-12-06 created schematic
    [can.kicad_sch, mcu.kicad_sch, pcb.kicad_pcb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]
2023-12-07 continued work on schematic
    [can.kicad_sch, mcu.kicad_sch, pcb.kicad_sch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]
2023-12-27 changed mcu layout to allow all desired features. added stm32 to schematic
    [mcu.kicad_sch, pcb.kicad_sch]
2023-12-29 enabled canbus interrupt
2024-01-14 schematic mostly done
    [can.kicad_sch, mcu.kicad_sch, pcb.kicad_sch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]
2024-01-14 created schematic pdf
2024-01-22 started work on layout
    [can.kicad_sch, mcu.kicad_sch, pcb.kicad_pcb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]
2024-01-24 canbus seems to work both ways now
2024-01-25 canbus now changes servo pwm
2024-01-29 adc value now being sent over canbus
2024-02-21 got multiple channels to work somehow. tried to add blinking to error handler
    [main.c]
2024-02-22 changed servo pwm prescaler so that the whole range should be within 2000
2024-02-28 changed servo timings and communication to be microseconds instead of something arbitrary
2024-03-26 fixed 5V being GND net
    [can.kicad_sch, pcb.kicad_pcb, pcb.kicad_sch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]
2024-04-24 removed FTDI and SBUS headers for now
    [mcu.kicad_sch, pcb.kicad_sch]
2024-04-24 added can+pwr header, worked layout
    [pcb.kicad_pcb, pcb.kicad_sch]
2024-04-25 added DIP switches, footprints
    [can.kicad_sch, mcu.kicad_sch, pcb.kicad_pcb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]
2024-05-01 updated components. worked on layout
    [mcu.kicad_sch, pcb.kicad_pcb, pcb.kicad_sch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]
2024-05-03 added missing footprints
    [mcu.kicad_sch, pcb.kicad_pcb, power-supply.kicad_sch]
2024-05-07 worked on layout
    [pcb.kicad_pcb, power-supply.kicad_sch]
2024-05-16 worked on layout. changed JTAG pinout and changed it to bottomside test-points
    [mcu.kicad_sch, pcb.kicad_pcb]
2024-05-20 removed RTC crystal, started routing
    [mcu.kicad_sch, pcb.kicad_pcb]
2024-05-21 routing completed
    [mcu.kicad_sch, pcb.kicad_pcb, pcb.kicad_sch]
2024-05-21 updated pcb documentation
    [can.kicad_sch, mcu.kicad_sch, pcb.kicad_pcb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]
2024-05-28 added resistor to tweak step-down low-voltage range. flipped trimmer polarity
    [pcb.kicad_pcb, power-supply.kicad_sch]
2024-05-29 minor tweaks on battery current paths
    [pcb.kicad_pcb]
2024-06-05 servo control now resets to middle if they aren't updated often enough
    [main.c]
2024-07-02 circuit seems to kill buck module at 14 V. even when installed as a dead bug
    [power-supply.kicad_sch]
2024-07-16 changed current measurement offset resistor values
    [power-supply.kicad_sch]
2024-08-06 updated component values
    [mcu.kicad_sch]
2024-08-14 swapped devboard to first version PCB. CAN doesn't send/receive properly
    [crawler-servo.ioc, main.c]
2024-08-15 rebuilt cubemx project and canbus works now
2024-08-15 cleanup, address dip switches now work, both ADC results are sent over CAN
2024-08-27 changed output connector to xt60 & 2x jst-xh-4
    [pcb.kicad_pcb, pcb.kicad_sch]
2024-09-17 fixed can packet length to 2 and can ID filtering
    [main.c]
2024-09-25 renamed ros node, was easier to delete and copy fixed code from elsewhere
    [rover.py]
2024-09-26 renamed node. changed channel numbering from 0-7 to 1-8 to match the pcb
2024-10-15 added kicad backups to gitignore
2024-10-22 worked on pinout
    [mcu.kicad_sch, pcb.kicad_pcb, pcb.kicad_sch]
2024-10-23 wattHours can now be set, no need to clamp to zero
2024-10-29 added hierarchial sheets for buffering
    [buffer.kicad_sch, input-buffers.kicad_sch, mcu.kicad_sch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]
2024-10-29 updated schematic pdf
2024-11-19 added buffer
    [buffer.kicad_sch]
2024-12-17 cleaned up buffer hierarchy
    [buffer.kicad_sch, input-buffers.kicad_sch, output-buffers.kicad_sch]
2025-01-21 added power switch for servos
    [input-buffers.kicad_sch, output-buffers.kicad_sch, servo-psu.kicad_sch]
2025-02-25 worked on layout. changed step-down module
    [pcb.kicad_pcb, power-supply.kicad_sch]
2025-03-21 updated xt60 footprint
    [pcb.kicad_pcb]
2025-03-28 fixed reversed sensor signals
    [pcb.kicad_pcb, pcb.kicad_sch]
2025-04-08 changed CAN driver
    [can.kicad_sch, pcb.kicad_pcb, pcb.kicad_sch]
2025-04-22 changed dip switch to rotary type
    [pcb.kicad_pcb, pcb.kicad_sch]
2025-05-27 worked on layout, added power to sensor connectors
    [pcb.kicad_pcb, pcb.kicad_sch]

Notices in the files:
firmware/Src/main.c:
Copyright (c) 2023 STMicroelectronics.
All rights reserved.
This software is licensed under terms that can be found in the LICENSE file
